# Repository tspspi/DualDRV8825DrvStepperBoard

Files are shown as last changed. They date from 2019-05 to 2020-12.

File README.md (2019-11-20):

# Dual stepper driver board (ATMEGA328P, DRV8825)

This repository contains sourcefiles and schematics for a DRV8825 based
dual stepper driver board. The stepper control algorithm is implemented
on an ATMega328P. The code is compatible with avr-gcc (see Makefile) and
the Arduino IDE (one has to ```#define ARDUINO 1``` to use code for the
Arduino platform).

This controller is thought to be used in robotic and CNC applications.
Some features make it useable as cruise control controller for small
robots that use steppers instead of other brushed or brushless motors
and which may require precise control over speed / sometimes precise control
over their position.

Since the controller uses I2C it can be controlled from 3.3V and 5V
devices without any level shifters (if pullups are only present to 3.3V
but not 5V vcc).

__The controller is currently work in progress (but usable). Functions that
have been tested won't change behaviour__

__Correctness proof is currently work in progress__

The stepper driver can be controlled via I2C and supports:

* Running at a constant speed
* Accelerated linear movement from one position to another
  position (stop to stop) as needed in many CNC applications
* Hold position (enable drivers, no movement)
* Free-wheeling (disable drivers)
* Accelerating or decelerating to another speed
* Emergency stop / Emergency stop with hold

Additional features:

* Commands and status via I2C to support up to 127 stepper
  driver boards (i.e. up to 254 steppers) per I2C bus.
* Runtime modification of acceleration/deceleration as well as
  maximum speed.
* Runtime reconfiguration of microstepping
* A configurable depth command queue (default 10 commands per channel)
* Aborting running commands
* Keeping track of current position (if enabled - useful for CNC applications)
* Keeping track of current speed

* Static analysis using frama-c and ACSL annotation is used to proof that the
  code is free of many known common runtime errors, numeric overflows/underflows,
  does only access valid memory, etc. and fulfills some properties (proofed by
  using an proof assistant). This is currently work in progress.

## Implementation status of I2C commands

|  Command | Implemented | Tested | Description | Comments |
| --- | --- | --- | --- | --- |
| Group 0: Configuration |
| i2cCmd_GetAccelerateDecelerate  	|  Y | Y |  8 byte payload Slave -> Master + 1 Byte Status | |
| i2cCmd_SetAccelerateDecelerate  	|  Y |  |  8 Byte payload Master -> Slave |  | |
| i2cCmd_GetVMax  					|  Y |  |  4 byte payload Slave -> Master + 1 Byte Status |  | |
| i2cCmd_SetVMax  					|  Y |  |  4 Byte payload Mater -> Slave | |
| i2cCmd_GetAlpha  					|  Y |  |  4 Byte payload Slave -> Master + 1 Byte Status | |
| i2cCmd_SetAlpha  					|  Y |  |  4 Byte payload Master -> Slave | |
| i2cCmd_GetMicrostepping  			|  Y |  |  1 Byte payload Slave -> Master (2x 3 Bit) + 1 Byte Status | |
| i2cCmd_SetMicrostepping  			|  Y | Y |  1 Byte payload Master -> Slave | Note: Currently microstepping does __not__ rescale step size (alpha) automatically |
| i2cCmd_GetFault  					|  Y |  |  1 Byte payload Master -> Slave (IS status) | |
| i2cCmd_RecalculateConstants  		|  Y |  |  Used to trigger recalculation of all constants (expensive operation; system should be stopped) | |
| Group 1: Queue |
| i2cCmd_GetCommandQueueSize  		|  Y |  |  Get size (first byte) and unused entires (second byte) of command queue + 1 Byte status | |
| Group 2: Enqueue commands |
| i2cCmd_Queue_Sync  				|  |  |  Sync. point; 1 Byte Channel | |
| i2cCmd_Queue_ConstSpeed  			|  Y | Y |  Constant speed; 1 Byte Channel; 4 Byte Speed | |
| i2cCmd_Queue_MoveTo  				|  Y | Y |  Move To (accelerated); 1 Byte Channel; 4 Byte Position | |
| i2cCmd_Queue_ConstSpeedAccel  	| Y | Y |  Constant speed with acceleration/deceleration; 1 Byte channel; 4 Byte speed | |
| i2cCmd_Queue_Hold  				|  Y | Y |  Hold position; 1 byte channel | |
| i2cCmd_Queue_DisableDrv  			|  Y | Y |  Disable drivers; 1 byte channel (both have to be ordered to disable to be effective) | |
| Group 3: Execute commands immedately |
| i2cCmd_Exec_Sync  				|  |  |  Sync. point; 1 Byte Channel | |
| i2cCmd_Exec_ConstSpeed  			|  Y | Y |  Constant speed; 1 Byte Channel; 4 Byte Speed | |
| i2cCmd_Exec_MoveTo  				|  Y | Y |  Move To (accelerated); 1 Byte Channel; 4 Byte Position | |
| i2cCmd_Exec_ConstSpeedAccel  		| Y | Y |  Constant speed with acceleration/deceleration; 1 Byte channel; 4 Byte speed | |
| i2cCmd_Exec_Hold  				|  Y | Y |  Hold position; 1 byte channel | |
| i2cCmd_Exec_DisableDrv  			|  Y | Y |  Disable drivers; 1 byte channel (both have to be ordered to disable to be effective) | |
| Group F: Emergency commands |
| i2cCmd_EmergencyStop  			|  Y |  |  Keeps motors engaged but stopped | Drivers stay engaged so current will keep flowing |
| i2cCmd_EmergencyOff  				|  Y |  |  Keeps motors disabled | Since drivers are disabled motors are free to turn freely (inertia!) |

## Host library

The host library (controller) has been currenty implemented and tested
on FreeBSD (especially on the RaspberryPi platform). Example usage can
be seen in the ```controller/tests``` directory.

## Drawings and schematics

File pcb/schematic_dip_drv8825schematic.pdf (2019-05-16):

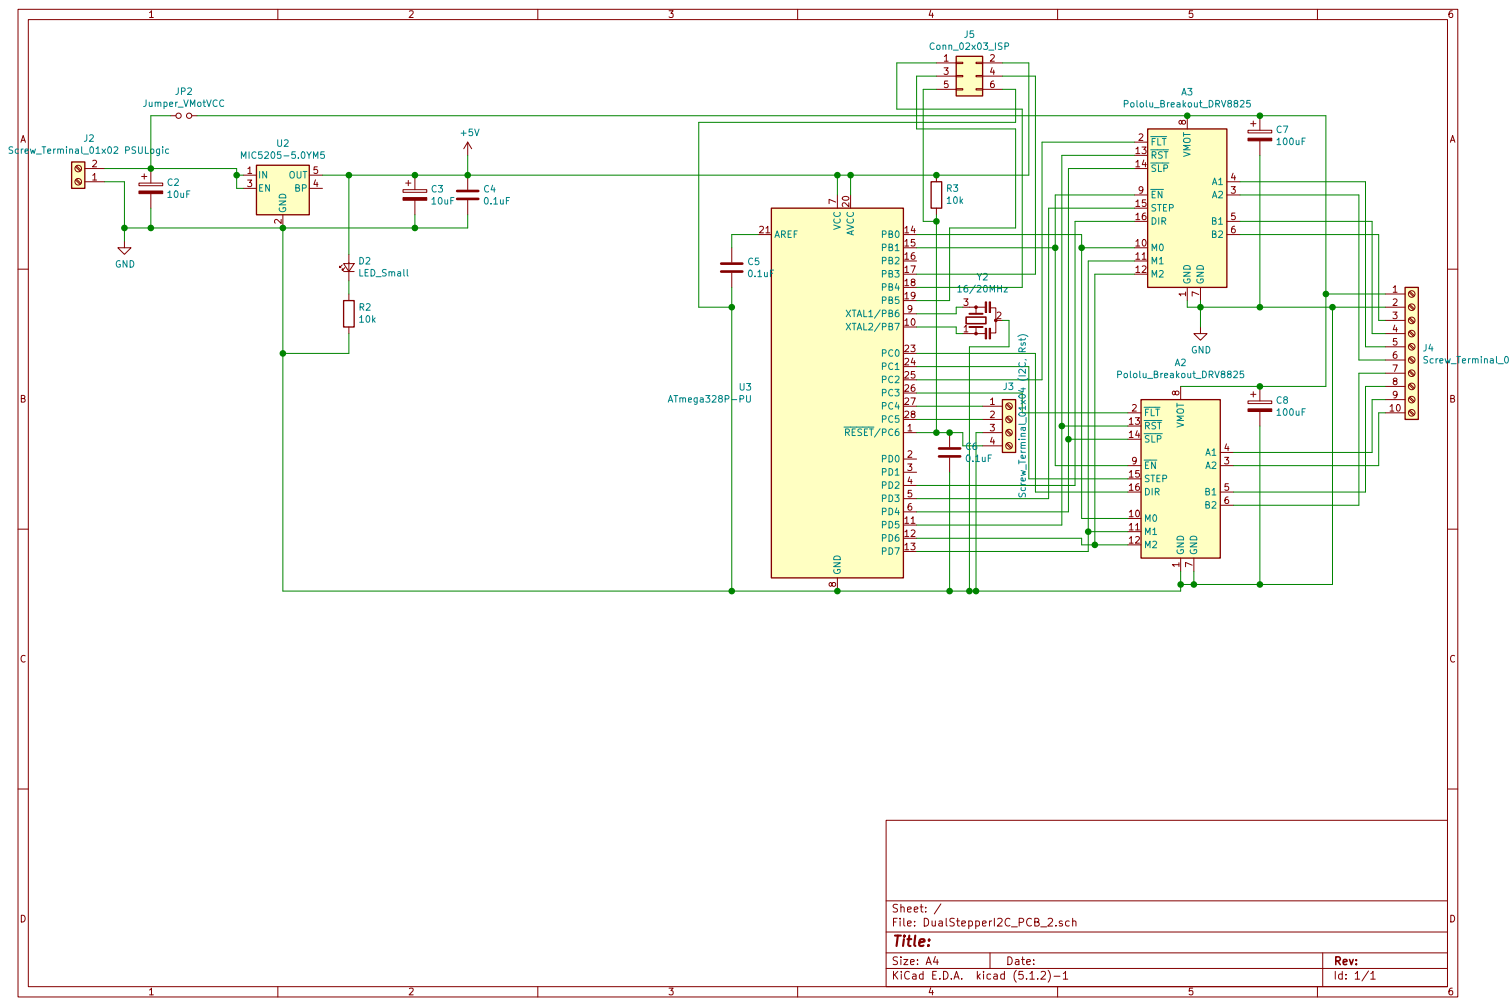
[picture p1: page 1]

1 M0 10 M1 11 M2 12 RST 13 SLP 14 STEP 15 DIR 16 FLT 2 A2 3 A1 4 B1 5 B2 6 GND

4 | J4Screw_Terminal_01x10 (Stepper) GND

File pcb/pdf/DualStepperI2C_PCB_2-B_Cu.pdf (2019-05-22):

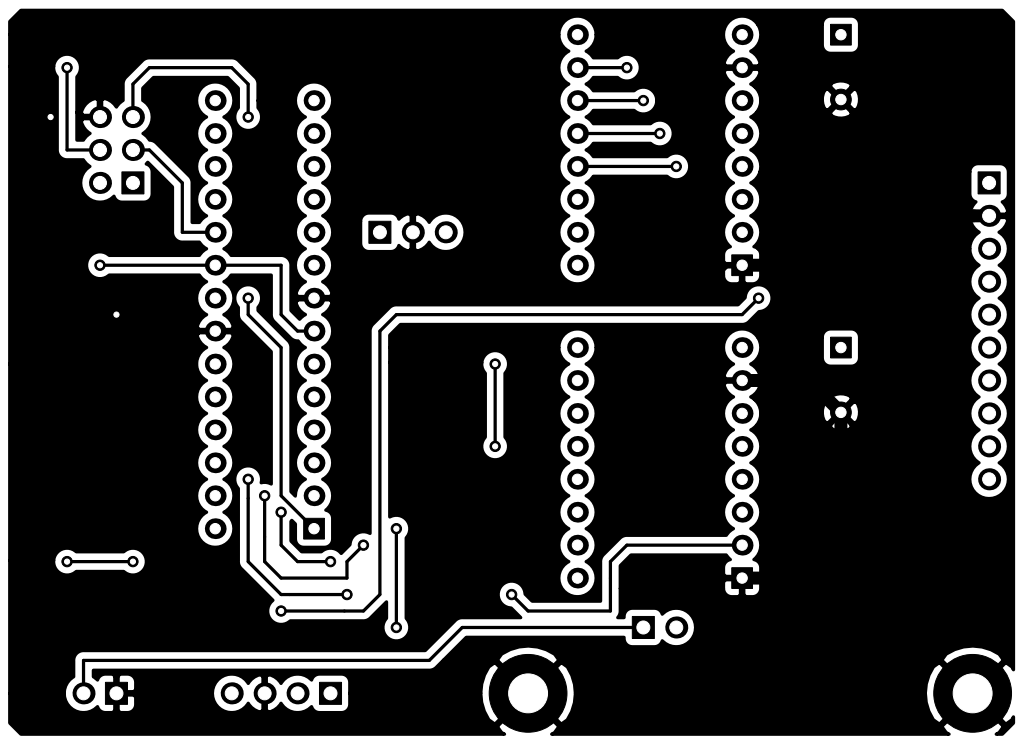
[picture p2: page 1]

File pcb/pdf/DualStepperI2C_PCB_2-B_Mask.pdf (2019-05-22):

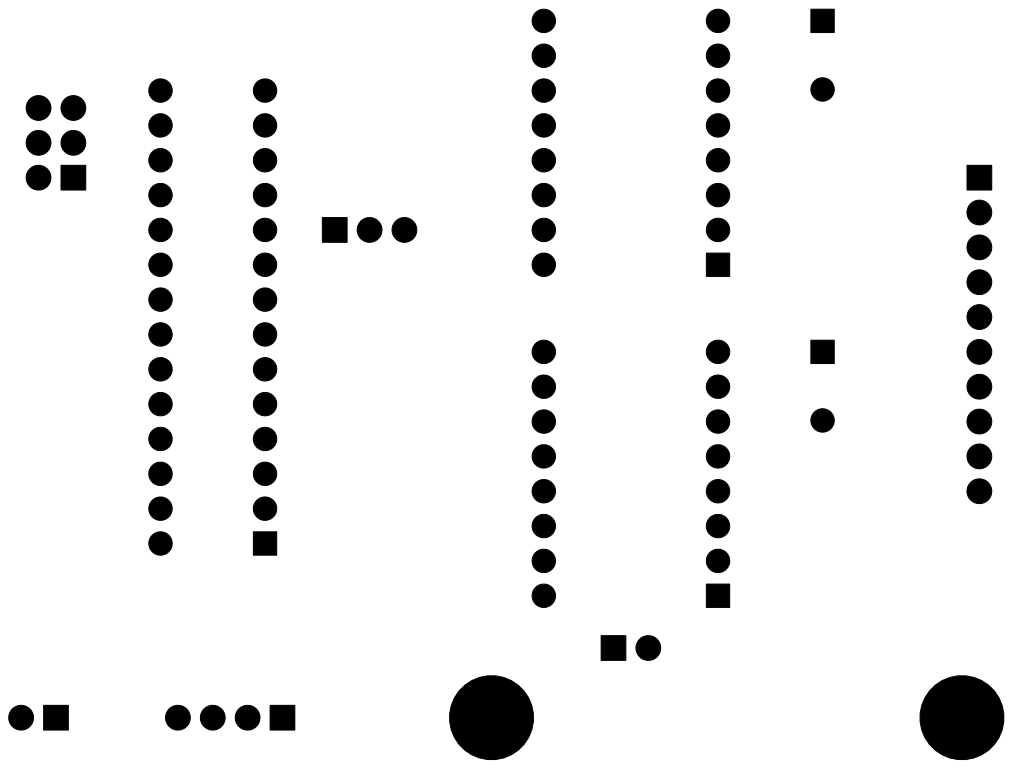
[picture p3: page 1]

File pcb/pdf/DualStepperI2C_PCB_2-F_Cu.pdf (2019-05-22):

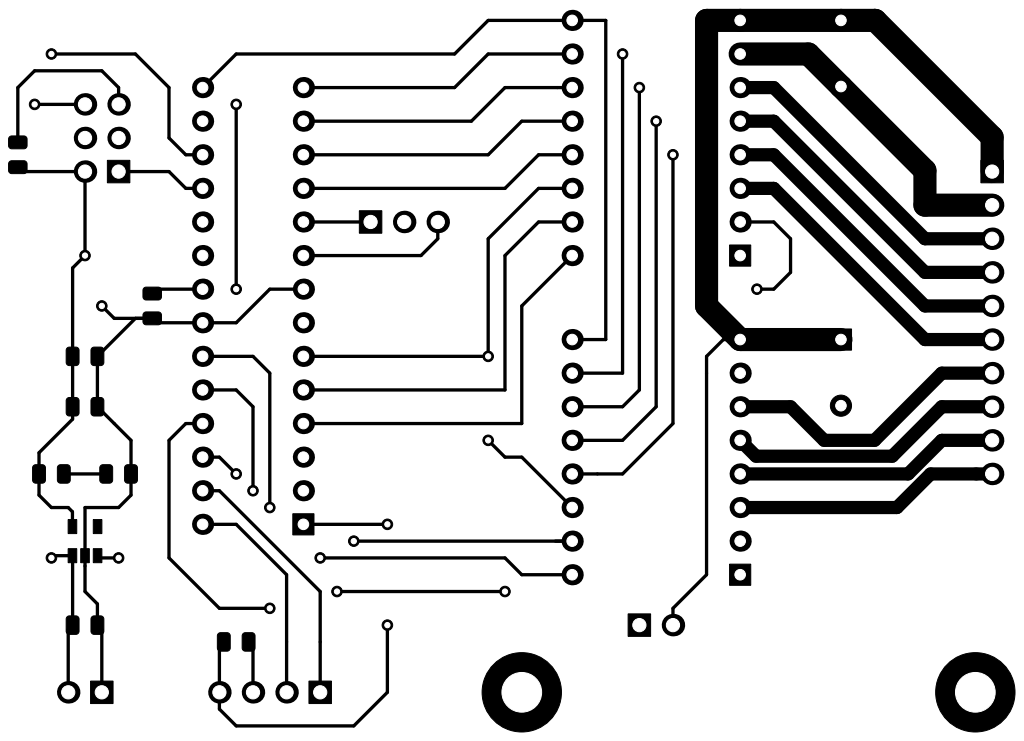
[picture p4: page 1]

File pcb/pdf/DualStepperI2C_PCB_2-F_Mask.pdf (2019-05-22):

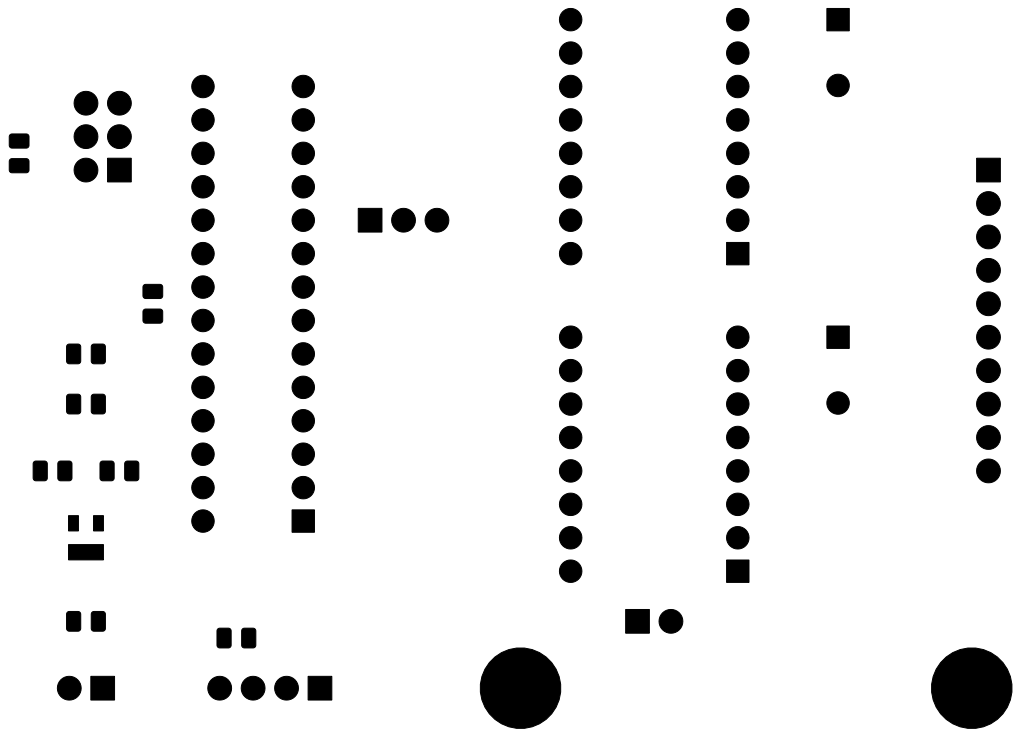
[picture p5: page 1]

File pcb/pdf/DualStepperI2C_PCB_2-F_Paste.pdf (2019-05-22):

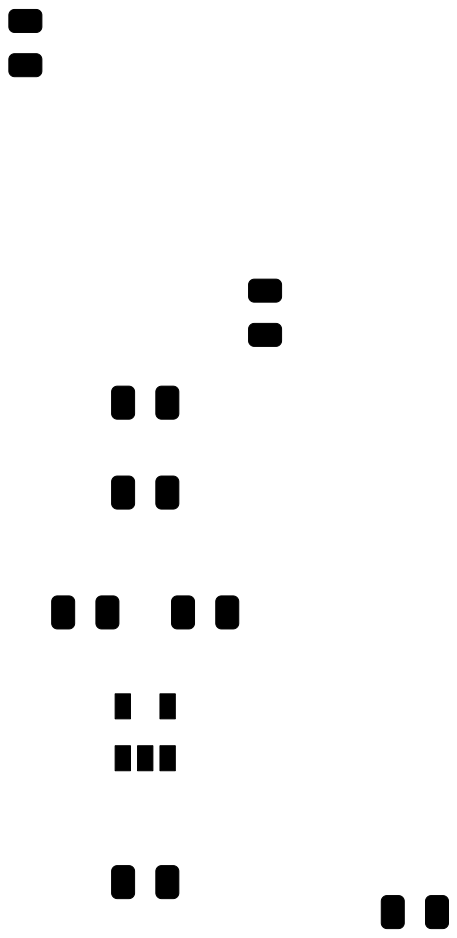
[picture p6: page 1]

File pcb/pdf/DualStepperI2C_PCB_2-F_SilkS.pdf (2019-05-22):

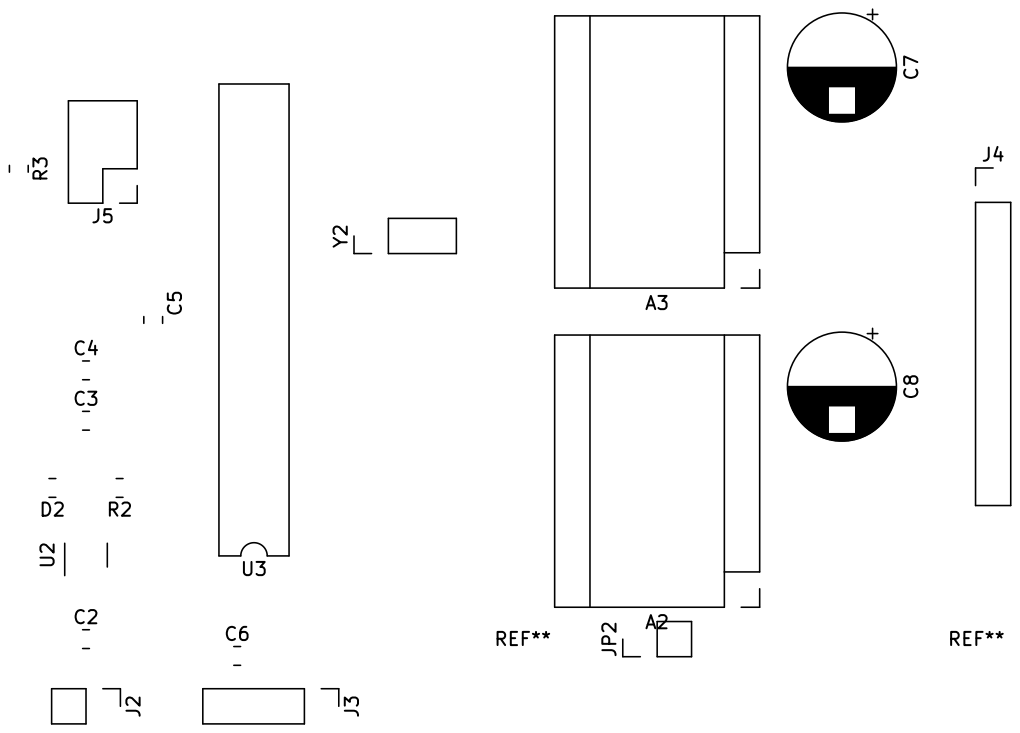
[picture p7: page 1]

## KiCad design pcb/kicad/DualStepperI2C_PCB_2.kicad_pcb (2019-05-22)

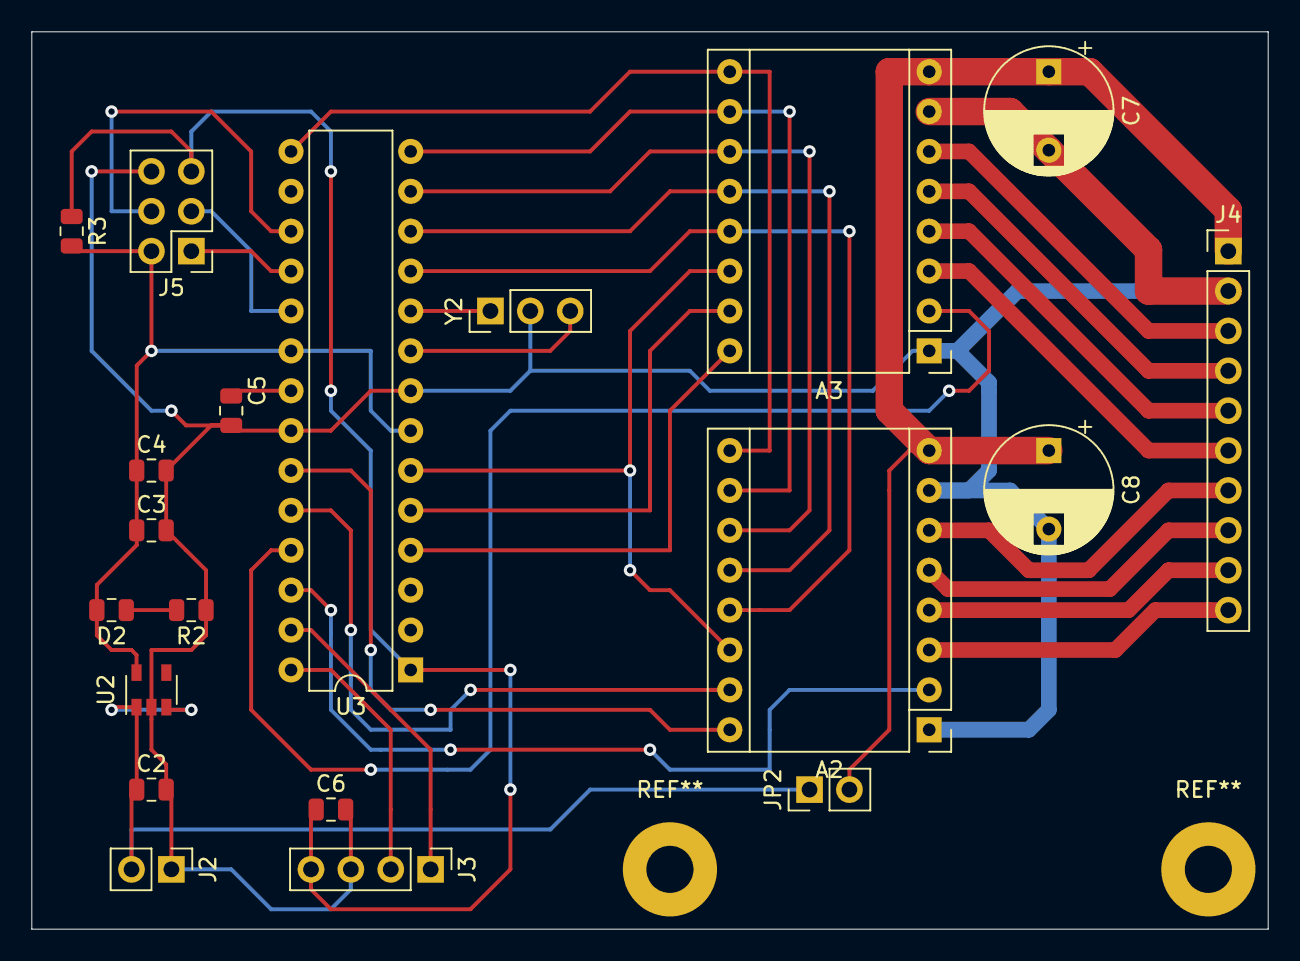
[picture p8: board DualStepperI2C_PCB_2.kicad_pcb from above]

Board: 2 copper layers, 78.7 x 57.1 mm, 20 parts (0 on the bottom side), 34 nets.

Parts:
A2, A3: Pololu_Breakout_DRV8825; Pololu_Breakout-16_15.2x20.3mm
C2, C3: 10uF; C_0805_2012Metric
C4, C5, C6: 0.1uF; C_0805_2012Metric
C7, C8: 100uF; CP_Radial_D8.0mm_P5.00mm
D2: LED_Small; C_0805_2012Metric
J2: Screw_Terminal_01x02 PSULogic; PinHeader_1x02_P2.54mm_Vertical
J3: Screw_Terminal_01x04 (I2C, Rst); PinHeader_1x04_P2.54mm_Vertical
J4: Screw_Terminal_01x10 (Stepper); PinHeader_1x10_P2.54mm_Vertical
J5: Conn_02x03_ISP; PinHeader_2x03_P2.54mm_Vertical
JP2: Jumper_VMotVCC; PinHeader_1x02_P2.54mm_Vertical
R2, R3: 10k; R_0805_2012Metric
U2: MIC5205-5.0YM5; SOT-23-5
U3: ATmega328P-PU; DIP-28_W7.62mm
Y2: 16/20MHz; PinHeader_1x03_P2.54mm_Vertical

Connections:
+5V: C3.1, C4.1, D2.2, J5.2, R3.2, U2.5, U3.7, U3.20
GND: A2.1, A2.7, A3.1, A3.7, C2.2, C3.2, C4.2, C5.2, C6.2, C7.2, C8.2, J2.1, J3.3, J4.2, J5.6, R2.1, U2.2, U3.8, U3.22, Y2.2
unnamed: A2.2, U3.26
unnamed: A2.3, J4.10
unnamed: A2.4, J4.9
unnamed: A2.5, J4.8
unnamed: A2.6, J4.7
unnamed: A2.8, A3.8, C7.1, C8.1, J4.1, JP2.2
unnamed: A2.9, A3.9, U3.15
unnamed: A2.10, A3.10, U3.14
unnamed: A2.11, A3.11, U3.13
unnamed: A2.12, A3.12, U3.12
unnamed: A2.13, A3.13, U3.11
unnamed: A2.14, A3.14, U3.6
unnamed: A2.15, U3.24
unnamed: A2.16, U3.23
unnamed: A3.2, U3.25
unnamed: A3.3, J4.6
unnamed: A3.4, J4.5
unnamed: A3.5, J4.4
unnamed: A3.6, J4.3
unnamed: A3.15, U3.5
unnamed: A3.16, U3.4
unnamed: C2.1, J2.2, JP2.1, U2.1, U2.3
unnamed: C5.1, U3.21
unnamed: C6.1, J3.4, J5.5, R3.1, U3.1
unnamed: D2.1, R2.2
unnamed: J3.1, U3.27
unnamed: J3.2, U3.28
unnamed: J5.1, U3.18
unnamed: J5.3, U3.19
unnamed: J5.4, U3.17
unnamed: U3.9, Y2.3
unnamed: U3.10, Y2.1

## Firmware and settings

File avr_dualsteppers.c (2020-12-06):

#include <avr/io.h>
#include <avr/interrupt.h>
#include <math.h>
#include <util/twi.h>
#include <stdint.h>

#define DEBUG

#ifndef STEPPER_I2C_ADDRESS
	#define STEPPER_I2C_ADDRESS 0x14
#endif
#ifndef M_PI
	#define M_PI 3.14159265358979323846264338327950288
#endif

/*
	If the following preprocessor directive is defined the steppers
	will be put in sleep mode upon reset (after initial power-up)
*/
#define STEPPER_DISABLE_STARTUP 1

#ifndef __cplusplus
	typedef int bool;
	#define true 1
	#define false 0
#endif

/*
	Pin usage:
		pinDir1		2	PD2		OUT
		pinStep1	3	PD3		OUT

		pinFault1	16	PC2		IN		PCINT10 (PCI1)
		pinDir2		14	PC0		OUT
		pinStep2	15	PC1		OUT
		pinFault2	17	PC3		IN		PCINT11 (PCI1)

		pinSleep    4	PD4		OUT
		pinReset    5	PD5		OUT
		pinMode2    6	PD6		OUT
		pinMode1    7	PD7		OUT

		pinMode0    8	PB0		OUT
		pinEnable   9	PB1		OUT


	I/O bank configuration:
		PB:		0	OUT		LOW (Fullstep)
				1	OUT		HIGH (ENABLE)
				2	IN		no pull
				3	IN		no pull
				4	IN		no pull
				5	IN		no pull
				6	IN		no pull
				7	IN		no pull

				DDRB = 0x03;
				PORTB = 0x02;

		PC:		0	OUT		LOW
				1	OUT		LOW
				2	IN		no pull
				3	IN		no pull
				4	IN		no pull
				5	IN		no pull
				6	IN		no pull
				7	IN		no pull

				DDRC = 0x03;
				PORTC = 0x00;

		PD:		0	IN		no pull
				1	IN		no pull
				2	OUT		LOW (Dir)
				3	OUT		LOW (Step)
				4	OUT		LOW (SLEEP)
				5	OUT		LOW (RESET)
				6	OUT		LOW (Fullstep)
				7	OUT		LOW (Fullstep)

				DDRD = 0xFC;
				PORTD = 0x00;
*/

/*
	Master clock source will be TIMER2

	Running with one of the following settings:
		Prescaler		Frequency		OCR1A		Effective Pulse Frequency
		/64				250 kHz			2			62.5 kHz
		/256			62.5 kHz		1			31.2 kHz
		/1024			15.625 kHz		1			7.812 kHz
*/

#ifndef STEPPER_COMMANDQUEUELENGTH
	#define STEPPER_COMMANDQUEUELENGTH 10
#endif

#define STEPPER_TIMERTICK_FRQ 			7812/2
#define STEPPER_TIMERTICK_PRESCALER		0x06
#define STEPPER_TIMERTICK_OVERFLOWVAL	0x01
#define STEPPER_WAKEUP_SLEEP_TICKS		10			/* More than 1.2 ms! */

/*
#define STEPPER_INITIAL_ALPHA			(0.01 * M_PI)
#define STEPPER_INITIAL_VMAX			(83.0 * M_PI)
#define STEPPER_INITIAL_ACCELERATION	(18.0 * M_PI)
#define STEPPER_INITIAL_DECELERATION	(-18.0 * M_PI)
*/
#define STEPPER_INITIAL_ALPHA			(0.01 * M_PI)
#define STEPPER_INITIAL_VMAX			6
#define STEPPER_INITIAL_ACCELERATION	1 /* 6 */
#define STEPPER_INITIAL_DECELERATION	-1 /* -6 */
#define STEPPER_INITIAL_MICROSTEPPING	0

/*
	Min and max configureable values
		Alpha:		Step size in radians
		V_max:		Maximum speed in radians per second
					Note: Since max. 250 kHz stepping frequency
						is supported by DRV8825 we use this as
						the limit together with alpha.

						(Alpha * 250 000)
		a, d		Acceleration and deceleration in radians per
					squaresecond
*/
#define STEPPER_MAX_ALPHA					(0.01 * M_PI)
#define STEPPER_MIN_ALPHA					((0.01 * M_PI)/128.0)
#define STEPPER_MAX_VMAX					100 /* (STEPPER_MAX_ALPHA * 250000.0) */
#define STEPPER_MIN_VMAX					0.01
// #define STEPPER_MIN_ACCELERATION			0.01 /* Currently arbitrary! */
// #define STEPPER_MAX_ACCELERATION			((STEPPER_MAX_VMAX * STEPPER_MAX_VMAX)/(STEPPER_MIN_ALPHA*4294967296.0))
#define STEPPER_MIN_ACCELERATION			((STEPPER_MAX_VMAX * STEPPER_MAX_VMAX)/(STEPPER_MIN_ALPHA*4294967296.0))
#define STEPPER_MAX_ACCELERATION			1000 /* Currently arbitrary */
#define STEPPER_MIN_DECELERATION			(-1.0 * ((STEPPER_MAX_VMAX * STEPPER_MAX_VMAX)/(STEPPER_MIN_ALPHA*4294967296.0)))
#define STEPPER_MAX_DECELERATION			-0.01 /* Currently arbitrary! */

#define STEPPER_MIN_RELATIVEDISTANCE		STEPPER_MIN_ALPHA
#define STEPPER_MAX_RELATIVEDISTANCE		(4294967295.0 * STEPPER_MIN_ALPHA)

/*
	We use our own systick implementation
*/
unsigned long int millis();
unsigned long int micros();
void delay(unsigned long millisecs);
void delayMicros(unsigned int microDelay);

enum stepperCommandType {
	stepperCommand_AccelerateStopToStop,
	stepperCommand_ConstantSpeed,
	stepperCommand_Stop,
	stepperCommand_Disable,
	stepperCommand_AccelerateToSpeed,
	stepperCommand_DecelerateToSpeed,
};

struct stepperCommand {
	enum stepperCommandType		cmdType;
	int 						forward;
	union {
		struct {
			uint32_t			nA;
			uint32_t			nC;
			uint32_t			nD;

			double				c7, c8, c9; /* Calculation constants for our specific acceleration and deceleration. */

			double				initialDelayTicks;
		} acceleratedStopToStop;
		struct {
			uint32_t			cConst; /* In case of constant speed mode we supply the tick count per constant step */
		} constantSpeed;
		struct {
			uint32_t			nA;
			uint32_t			nD;

			double				c8, c9;
			double				cEnd;
			double				cStart;
		} accelerateDecelerateToConstSpeed;
	} data;
};

/*
	Command queue is a ringbuffer. Head points always to the next entry
	that is available for writing. If head == tail the queue is EMPTY!

	Tail is only ever advanced by TIMER2_COMPA_vect, head only ever by
	the motion planner.

	If Head + 1 == Tail the queue is currently FULL and nothing can
	be enqueued.
*/
struct stepperState {
	double							c_i;				/* The previously loaded c_i (used during calculation and advancing) */
	uint32_t						counterCurrent;		/* Counter reduced every time until we reach zero */

	struct stepperCommand			cmdQueue[STEPPER_COMMANDQUEUELENGTH];
	unsigned int					cmdQueueHead;
	unsigned int					cmdQueueTail;

	#ifdef ENABLE_ABSOLUTEPOSITION
		long int						currentPosition;			/* Current position in "steps" i.e. currentPosition * alpha = angular Position */
	#endif

	/* Cache for precalculated constants - see documentation */
	struct {
		double						c1;
		double						c2;
		double						c3;
		double						c4;
		double						c5;

		double						c7;
		double						c8;
		double						c9;
		double						c10;
	} constants;

	struct {
		double						acceleration; /* in rad/sec */
		double						deceleration; /* in rad/sec */
		double						alpha; /* step size in rad */
		double						vmax; /* in rad/sec */
	} settings;
};

#define STEPPER_COUNT 2

/*
	Declare state for both steppers
*/
static struct stepperState			state[STEPPER_COUNT];
static uint8_t						stateMicrostepping;
volatile static uint8_t				stateFault;
static uint8_t						drvEnableState;
static uint8_t						drvRealEnabled;

bool bResetRun = false;
static volatile bool bIntTriggered = false;

/*@
	requires \valid(&PORTC) && \valid(&PORTD);

	assigns drvRealEnabled;
	assigns bIntTriggered;

	assigns PORTC, PORTD;

	ensures
		\forall integer iStep; 0 <= iStep < STEPPER_COUNT
		==> (state[iStep].cmdQueueHead >= 0) && (state[iStep].cmdQueueHead < STEPPER_COMMANDQUEUELENGTH);
	ensures
		\forall integer iStep; 0 <= iStep < STEPPER_COUNT
		==> (state[iStep].cmdQueueTail >= 0) && (state[iStep].cmdQueueTail < STEPPER_COMMANDQUEUELENGTH);
*/
static void handleTimer2Interrupt() {
	if(!bIntTriggered) {
		return;
	}
	bIntTriggered = false;

	/*
		Re-enable counter. This is used to delay the
		next stepper commands after re-awaking from
		sleep.
	*/
	if((drvRealEnabled & 0x7F) != 0) {
		drvRealEnabled = drvRealEnabled - 1;
		return;
	}

	/*
		Interrupt handler executed with 2 * STEPPER_TIMERTICK_FRQ frequency
		either use to disable step pins or advance state machine depending on
		out state. We have to finish in way less then 1024 ticks ...
	*/
	int stepperIdx;
	/*@
		loop assigns PORTD, PORTC;
		loop assigns drvRealEnabled, drvEnableState;
		loop assigns state[0 .. (STEPPER_COUNT-1)];

		loop invariant 0 <= stepperIdx < STEPPER_COUNT;

	*/
	for(stepperIdx = 0; stepperIdx < STEPPER_COUNT; stepperIdx = stepperIdx + 1) {
		if(bResetRun) {
			if(stepperIdx == 0) {
				// Pulse PD2 low
				PORTD = PORTD & (~0x08);
			} else {
				// Pulse PC1 low
				PORTC = PORTC & (~0x02);
			}

			if((drvEnableState == 0) && ((drvRealEnabled & 0x80) != 0)) {
				/* Put driver into sleep if none is enabled AND our current real enable state is not the same */
				drvRealEnabled = drvRealEnabled & 0x7F;
				PORTD = PORTD & (~0x10); /* Enter sleep state by pulling SLEEP LOW (enabled) */
			}
		} else {
			if(state[stepperIdx].cmdQueueTail == state[stepperIdx].cmdQueueHead) {
				/* Nothing to do ... */
				continue;
			}

			const int qIdx = state[stepperIdx].cmdQueueTail;
			if(state[stepperIdx].c_i == -1) {
				/* We wake up from idle ... any may have to do some initialization */
				if(stepperIdx == 0) {
					// PD2
					if(state[stepperIdx].cmdQueue[qIdx].forward != 0) {
						PORTD = PORTD | 0x04;
					} else {
						PORTD = PORTD & (~0x04);
					}
				} else {
					// PC0
					if(state[stepperIdx].cmdQueue[qIdx].forward != 0) {
						PORTC = PORTC | 0x01;
					} else {
						PORTC = PORTC & (~0x01);
					}
				}

				/* Check if drivers are disabled and we have to execute an command ... */
				if((drvRealEnabled & 0x80) == 0) {
					/* Steppers are disabled. Re-enable and wait for startup period */
					PORTD = PORTD | 0x10; /* Leave sleep state by pulling SLEEP HIGH (disabled) */
					drvRealEnabled = 0x80 | STEPPER_WAKEUP_SLEEP_TICKS;
					drvEnableState = drvEnableState | (1 << stepperIdx);
					break; // Next stepper as usual
				}

				if(state[stepperIdx].cmdQueue[qIdx].cmdType == stepperCommand_AccelerateStopToStop) {
					state[stepperIdx].c_i = state[stepperIdx].cmdQueue[qIdx].data.acceleratedStopToStop.initialDelayTicks;
					if(state[stepperIdx].c_i > 4294967295.0) {
						state[stepperIdx].counterCurrent = ~0;
					} else if(state[stepperIdx].c_i < 1.0) {
						state[stepperIdx].counterCurrent = 1;
					} else {
						state[stepperIdx].counterCurrent = (uint32_t)state[stepperIdx].c_i;
					}
				} else if(state[stepperIdx].cmdQueue[qIdx].cmdType == stepperCommand_ConstantSpeed) {
					state[stepperIdx].c_i = state[stepperIdx].cmdQueue[qIdx].data.constantSpeed.cConst;
					state[stepperIdx].counterCurrent = state[stepperIdx].cmdQueue[qIdx].data.constantSpeed.cConst;
				} else if(state[stepperIdx].cmdQueue[qIdx].cmdType == stepperCommand_Disable) {
					drvEnableState = drvEnableState & (~(0x01 << stepperIdx));
					/* Switch to next state at next interrupt */
					state[stepperIdx].cmdQueueTail = (state[stepperIdx].cmdQueueTail + 1) % STEPPER_COMMANDQUEUELENGTH;
					state[stepperIdx].c_i = -1; /* This will initialize the next state as soon as it is available */
					continue;
				} else if(state[stepperIdx].cmdQueue[qIdx].cmdType == stepperCommand_Stop) {
					/*
						Our driver has already been enabled since we do that whenever we
						reach an enqueued command. So simply remove this task from the task
						queue. As long as nothing has been enqueued the steppers will be
						engaged and stopped
					*/
					state[stepperIdx].cmdQueueTail = (state[stepperIdx].cmdQueueTail + 1) % STEPPER_COMMANDQUEUELENGTH;
					state[stepperIdx].c_i = -1; /* This will initialize the next state as soon as it is available */
					continue;
				} else if((state[stepperIdx].cmdQueue[qIdx].cmdType == stepperCommand_AccelerateToSpeed) || (state[stepperIdx].cmdQueue[qIdx].cmdType == stepperCommand_DecelerateToSpeed)) {
					state[stepperIdx].c_i = state[stepperIdx].cmdQueue[qIdx].data.accelerateDecelerateToConstSpeed.cStart;
					if(state[stepperIdx].c_i > 4294967295.0) {
						state[stepperIdx].counterCurrent = ~0;
					} else if(state[stepperIdx].c_i < 1.0) {
						state[stepperIdx].counterCurrent = 1;
					} else {
						state[stepperIdx].counterCurrent = (uint32_t)state[stepperIdx].c_i;
					}
				} else {
					continue;
				}
			} else if((state[stepperIdx].counterCurrent = state[stepperIdx].counterCurrent - 1) > 0) {
				/* Just advance our counter ... */
				continue;
			} else if(state[stepperIdx].cmdQueue[qIdx].cmdType == stepperCommand_AccelerateStopToStop) {
				if(state[stepperIdx].cmdQueue[qIdx].data.acceleratedStopToStop.nA > 0) {
					state[stepperIdx].c_i = state[stepperIdx].c_i / (1 + state[stepperIdx].constants.c8 * state[stepperIdx].c_i * state[stepperIdx].c_i);
					state[stepperIdx].cmdQueue[qIdx].data.acceleratedStopToStop.nA = state[stepperIdx].cmdQueue[qIdx].data.acceleratedStopToStop.nA - 1;

					/* c_i to counter value */
					if(state[stepperIdx].c_i > 4294967295.0) {
						state[stepperIdx].counterCurrent = ~0;
					} else if(state[stepperIdx].c_i < 1.0) {
						state[stepperIdx].counterCurrent = 1;
					} else {
						state[stepperIdx].counterCurrent = (uint32_t)state[stepperIdx].c_i;
					}
				} else if(state[stepperIdx].cmdQueue[qIdx].data.acceleratedStopToStop.nC > 0) {
					state[stepperIdx].cmdQueue[qIdx].data.acceleratedStopToStop.nC = state[stepperIdx].cmdQueue[qIdx].data.acceleratedStopToStop.nC - 1;

					/* c_i to counter value */
					if(state[stepperIdx].c_i > 4294967295.0) {
						state[stepperIdx].counterCurrent = ~0;
					} else if(state[stepperIdx].c_i < 1.0) {
						state[stepperIdx].counterCurrent = 1;
					} else {
						state[stepperIdx].counterCurrent = (uint32_t)state[stepperIdx].c_i;
					}
				} else if(state[stepperIdx].cmdQueue[qIdx].data.acceleratedStopToStop.nD > 0) {
					state[stepperIdx].c_i = state[stepperIdx].c_i / (1 + state[stepperIdx].constants.c9 * state[stepperIdx].c_i * state[stepperIdx].c_i);
					/* c_i to counter value */
					if(state[stepperIdx].c_i > 4294967295.0) {
						state[stepperIdx].counterCurrent = ~0;
					} else if(state[stepperIdx].c_i < 1.0) {
						state[stepperIdx].counterCurrent = 1;
					} else {
						state[stepperIdx].counterCurrent = (uint32_t)state[stepperIdx].c_i;
					}

					if((state[stepperIdx].cmdQueue[qIdx].data.acceleratedStopToStop.nD = state[stepperIdx].cmdQueue[qIdx].data.acceleratedStopToStop.nD - 1) == 0) {
						/* Switch to next state at next interrupt */
						state[stepperIdx].cmdQueueTail = (state[stepperIdx].cmdQueueTail + 1) % STEPPER_COMMANDQUEUELENGTH;
						state[stepperIdx].c_i = -1; /* This will initialize the next state as soon as it is available */
					}
				}
			} else if(state[stepperIdx].cmdQueue[qIdx].cmdType == stepperCommand_AccelerateToSpeed) {
				state[stepperIdx].c_i = state[stepperIdx].c_i / (1 + state[stepperIdx].constants.c8 * state[stepperIdx].c_i * state[stepperIdx].c_i);

				/* c_i to counter value */
				if(state[stepperIdx].c_i > 4294967295.0) {
					state[stepperIdx].counterCurrent = ~0;
				} else if(state[stepperIdx].c_i < 1.0) {
					state[stepperIdx].counterCurrent = 1;
				} else {
					state[stepperIdx].counterCurrent = (uint32_t)state[stepperIdx].c_i;
				}

				if((state[stepperIdx].cmdQueue[qIdx].data.accelerateDecelerateToConstSpeed.nA = state[stepperIdx].cmdQueue[qIdx].data.accelerateDecelerateToConstSpeed.nA - 1) == 0) {
					/* Switch to next state at next interrupt */
					state[stepperIdx].cmdQueueTail = (state[stepperIdx].cmdQueueTail + 1) % STEPPER_COMMANDQUEUELENGTH;
					state[stepperIdx].c_i = -1; /* This will initialize the next state as soon as it is available */
				}
			} else if(state[stepperIdx].cmdQueue[qIdx].cmdType == stepperCommand_DecelerateToSpeed) {
				state[stepperIdx].c_i = state[stepperIdx].c_i / (1 + state[stepperIdx].constants.c9 * state[stepperIdx].c_i * state[stepperIdx].c_i);

				/* c_i to counter value */
				if(state[stepperIdx].c_i > 4294967295.0) {
					state[stepperIdx].counterCurrent = ~0;
				} else if(state[stepperIdx].c_i < 1.0) {
					state[stepperIdx].counterCurrent = 1;
				} else {
					state[stepperIdx].counterCurrent = (uint32_t)state[stepperIdx].c_i;
				}

				if((state[stepperIdx].cmdQueue[qIdx].data.accelerateDecelerateToConstSpeed.nD = state[stepperIdx].cmdQueue[qIdx].data.accelerateDecelerateToConstSpeed.nD - 1) == 0) {
					/* Switch to next state at next interrupt */
					state[stepperIdx].cmdQueueTail = (state[stepperIdx].cmdQueueTail + 1) % STEPPER_COMMANDQUEUELENGTH;
					state[stepperIdx].c_i = -1; /* This will initialize the next state as soon as it is available */
				}
			} else if(state[stepperIdx].cmdQueue[qIdx].cmdType == stepperCommand_ConstantSpeed) {
				state[stepperIdx].counterCurrent = state[stepperIdx].c_i; // Counter reload ...
			}

			if(stepperIdx == 0) {
				// Pulse PD2 high
				PORTD = PORTD | 0x08;
				#ifdef ENABLE_ABSOLUTEPOSITION
					if((PORTD & 0x04) != 0) {
						if(state[0].currentPosition < 2147483647) {
							state[0].currentPosition++;
						}
					} else {
						if(state[0].currentPosition > 0) {
							state[0].currentPosition--;
						}
					}
				#endif
			} else {
				// Pulse PC1 high
				PORTC = PORTC | 0x02;
				#ifdef ENABLE_ABSOLUTEPOSITION
					if((PORTC & 0x01) != 0) {
						if(state[1].currentPosition < 2147483647) {
							state[1].currentPosition++;
						}
					} else {
						if(state[1].currentPosition > 0) {
							state[1].currentPosition--;
						}
					}
				#endif
			}
		}
	}
	bResetRun = !bResetRun;
}

/*@
	assigns bIntTriggered;
	ensures bIntTriggered == true;
*/
ISR(TIMER2_COMPA_vect) {
	bIntTriggered = true;
}

/*@
	requires \valid_read(&PINC);

	assigns stateFault;
*/
ISR(PCINT1_vect) {
	/*
		Update fault pins ...
	*/
	uint8_t faultPins = PINC;
	stateFault = stateFault | (((faultPins >> 2) & 0x01) ^ 0x01) | (((faultPins >> 2) & 0x02) ^ 0x02);
}
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
int main() {
	#ifndef FRAMAC_SKIP
		cli();
	#endif

	// Setup TIMER0 as our sysclk timer
	// TCCR0A = 0x02;		/* CTC mode */
	TCCR0A = 0x00;
	TCCR0B = 0x03;		/* /64 prescaler */
	TIMSK0 = 0x01;		/* Enable overflow interrupt */

	// Sysclk is now working - re-enable interrupts
	sei();

	#ifdef DEBUG
		// Signal bootup via LED
		DDRB = 0x20;
		PORTB = 0x20;
		delay(1000);
		PORTB = 0x00;
		delay(1000);
		PORTB = 0x20;
		delay(1000);
		PORTB = 0x00;
		delay(1000);
	#endif

	// Disable serial (enabled from bootloader)
	UCSR0B = 0;

	// Initialize I2C
	i2cSlaveInit(STEPPER_I2C_ADDRESS);

	// Stepper setup
	stepperSetup();

	/*
		Since we don't use "delay" in production any more we
		can disable TIMER0 again to reduce possible jitter
		of TIMER2.
	*/
	#ifndef DEBUG
		TIMSK0 = 0x00; /* Disable interrupts of TIMER0 */
	#endif

	for(;;) {
		/*
			Handle stepper events (NOT from ISR but synchronously)
		*/
		handleTimer2Interrupt();
		/*
			Execute I2C message loop
		*/
		i2cMessageLoop();
	}
}

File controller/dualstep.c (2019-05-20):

#include <stdlib.h>

#include "./dualstep.h"

#include <stdint.h>
#include <math.h>

#include "./serdeshelper.h"

#ifdef __cplusplus
	extern "C" {
#endif

enum stepperI2cCommand {
	i2cCmd_GetAccelerateDecelerate		= 0x01,	/* 8 byte payload Slave -> Master + 1 Byte Status */
	i2cCmd_SetAccelerateDecelerate		= 0x02,	/* 8 Byte payload Master -> Slave */
	i2cCmd_GetVMax						= 0x03, /* 4 byte payload Slave -> Master + 1 Byte Status */
	i2cCmd_SetVMax						= 0x04,	/* 4 Byte payload Mater -> Slave */
	i2cCmd_GetAlpha						= 0x05,	/* 4 Byte payload Slave -> Master + 1 Byte Status */
	i2cCmd_SetAlpha						= 0x06,	/* 4 Byte payload Master -> Slave */
	i2cCmd_GetMicrostepping				= 0x07, /* 1 Byte payload Slave -> Master (2x 3 Bit) + 1 Byte Status */
	i2cCmd_SetMicrostepping				= 0x08, /* 1 Byte payload Master -> Slave */

	i2cCmd_GetFault						= 0x0E, /* 1 Byte payload Master -> Slave (IS status) */
	i2cCmd_RecalculateConstants			= 0x0F, /* Used to trigger recalculation of all constants (expensive operation; system should be stopped) */



	i2cCmd_GetCommandQueueSize			= 0x10,	/* Get size (first byte) and unused entires (second byte) of command queue + 1 Byte status */



	i2cCmd_Queue_Sync					= 0x20,	/* Sync. point; 1 Byte Channel */
	i2cCmd_Queue_ConstSpeed				= 0x21,	/* Constant speed; 1 Byte Channel; 4 Byte Speed */
	i2cCmd_Queue_MoveTo					= 0x22,	/* Move To (accelerated); 1 Byte Channel; 4 Byte Position */
	i2cCmd_Queue_ConstSpeedAccel		= 0x23,	/* Constant speed with acceleration/deceleration; 1 Byte channel; 4 Byte speed */
	i2cCmd_Queue_Hold					= 0x2E,	/* Hold position; 1 byte channel */
	i2cCmd_Queue_DisableDrv				= 0x2F,	/* Disable drivers; 1 byte channel (both have to be ordered to disable to be effective) */

	i2cCmd_Exec_Sync					= 0x30,	/* Sync. point; 1 Byte Channel */
	i2cCmd_Exec_ConstSpeed				= 0x31,	/* Constant speed; 1 Byte Channel; 4 Byte Speed */
	i2cCmd_Exec_MoveTo					= 0x32,	/* Move To (accelerated); 1 Byte Channel; 4 Byte Position */
	i2cCmd_Exec_ConstSpeedAccel			= 0x33,	/* Constant speed with acceleration/deceleration; 1 Byte channel; 4 Byte speed */
	i2cCmd_Exec_Hold					= 0x3E,	/* Hold position; 1 byte channel */
	i2cCmd_Exec_DisableDrv				= 0x3F,	/* Disable drivers; 1 byte channel (both have to be ordered to disable to be effective) */

	i2cCmd_EmergencyStop				= 0xFE,	/* Keeps motors engaged but stopped */
	i2cCmd_EmergencyOff					= 0xFF, /* Keeps motors disabled */
};


static enum i2cDualStepperError i2cDual_Release(
	struct i2cDualStepper* lpSelf
) {
	if(lpSelf == NULL) { return i2cDualStepperErrorE_InvalidParam; }

	/*
		We do NOT stop, disengage drivers, etc. if not
		told explicitly!
	*/
	free(lpSelf);
	return i2cDualStepperErrorE_Ok;
}

static enum i2cDualStepperError i2cDual_GetAccelerationDeceleration(
	struct i2cDualStepper* lpSelf,
	unsigned long int dwChannel,
	double* lpAcceleration,
	double* lpDeceleration
) {
	enum i2cError i2e;

	if(lpSelf == NULL) { return i2cDualStepperErrorE_InvalidParam; }
	if(dwChannel > 1) { return i2cDualStepperErrorE_InvalidParam; }

	uint8_t req[2] = { i2cCmd_GetAccelerateDecelerate, (uint8_t)dwChannel };
	uint8_t resp[8];

	/* Perform query */
	i2e = i2cWriteRead(lpSelf->i2cBus, lpSelf->devAddr, req, sizeof(req), resp, sizeof(resp));
	if(i2e != i2cE_Ok) { return i2cDualStepperErrorE_IOError; }

	if(lpAcceleration != NULL) { (*lpAcceleration) = (double)deserializeIEEE754SingleFloat_4Bytes(&(resp[0])); }
	if(lpDeceleration != NULL) { (*lpDeceleration) = (double)deserializeIEEE754SingleFloat_4Bytes(&(resp[4])); }

	return i2cDualStepperErrorE_Ok;
}

static enum i2cDualStepperError i2cDual_SetAccelerationDeceleration(
	struct i2cDualStepper* lpSelf,
	unsigned long int dwChannel,
	double lpAcceleration,
	double lpDeceleration
) {
	enum i2cError i2e;

	if(lpSelf == NULL) { return i2cDualStepperErrorE_InvalidParam; }
	if(dwChannel > 1) { return i2cDualStepperErrorE_InvalidParam; }

	uint8_t req[2+8];
	req[0] = i2cCmd_SetAccelerateDecelerate;
	req[1] = (uint8_t)dwChannel;

	serializeIEEE754SingleFloat_4Bytes((float)lpAcceleration, &(req[2]));
	serializeIEEE754SingleFloat_4Bytes((float)lpDeceleration, &(req[2+4]));

	i2e = i2cWrite(lpSelf->i2cBus, lpSelf->devAddr, req, sizeof(req));
	if(i2e != i2cE_Ok) { return i2cDualStepperErrorE_IOError; }

	return i2cDualStepperErrorE_Ok;
}

static enum i2cDualStepperError i2cDual_GetVMax(
	struct i2cDualStepper* lpSelf,
	unsigned long int dwChannel,
	double* lpVMax
) {
	enum i2cError i2e;

	if(lpSelf == NULL) { return i2cDualStepperErrorE_InvalidParam; }
	if(dwChannel > 1) { return i2cDualStepperErrorE_InvalidParam; }

	uint8_t req[2] = { i2cCmd_GetVMax, (uint8_t)dwChannel };
	uint8_t resp[4];

	/* Perform query */
	i2e = i2cWriteRead(lpSelf->i2cBus, lpSelf->devAddr, req, sizeof(req), resp, sizeof(resp));
	if(i2e != i2cE_Ok) { return i2cDualStepperErrorE_IOError; }

	if(lpVMax != NULL) { (*lpVMax) = (double)deserializeIEEE754SingleFloat_4Bytes(&(resp[0])); }

	return i2cDualStepperErrorE_Ok;
}

static enum i2cDualStepperError i2cDual_SetVMax(
	struct i2cDualStepper* lpSelf,
	unsigned long int dwChannel,
	double vMax
) {
	enum i2cError i2e;

	if(lpSelf == NULL) { return i2cDualStepperErrorE_InvalidParam; }
	if(dwChannel > 1) { return i2cDualStepperErrorE_InvalidParam; }

	uint8_t req[2+4];
	req[0] = i2cCmd_SetVMax;
	req[1] = (uint8_t)dwChannel;

	serializeIEEE754SingleFloat_4Bytes((float)vMax, &(req[2]));

	i2e = i2cWrite(lpSelf->i2cBus, lpSelf->devAddr, req, sizeof(req));
	if(i2e != i2cE_Ok) { return i2cDualStepperErrorE_IOError; }

	return i2cDualStepperErrorE_Ok;
}
static enum i2cDualStepperError i2cDual_GetAlpha(
	struct i2cDualStepper* lpSelf,
	unsigned long int dwChannel,
	double* lpAlpha
) {
	enum i2cError i2e;

	if(lpSelf == NULL) { return i2cDualStepperErrorE_InvalidParam; }
	if(dwChannel > 1) { return i2cDualStepperErrorE_InvalidParam; }

	uint8_t req[2] = { i2cCmd_GetAlpha, (uint8_t)dwChannel };
	uint8_t resp[4];

	/* Perform query */
	i2e = i2cWriteRead(lpSelf->i2cBus, lpSelf->devAddr, req, sizeof(req), resp, sizeof(resp));
	if(i2e != i2cE_Ok) { return i2cDualStepperErrorE_IOError; }

	if(lpAlpha != NULL) { (*lpAlpha) = (double)deserializeIEEE754SingleFloat_4Bytes(&(resp[0])); }

	return i2cDualStepperErrorE_Ok;
}
static enum i2cDualStepperError i2cDual_SetAlpha(
	struct i2cDualStepper* lpSelf,
	unsigned long int dwChannel,
	double alpha
) {
	enum i2cError i2e;

	if(lpSelf == NULL) { return i2cDualStepperErrorE_InvalidParam; }
	if(dwChannel > 1) { return i2cDualStepperErrorE_InvalidParam; }

	uint8_t req[2+4];
	req[0] = i2cCmd_SetAlpha;
	req[1] = (uint8_t)dwChannel;

	serializeIEEE754SingleFloat_4Bytes((float)alpha, &(req[2]));

	i2e = i2cWrite(lpSelf->i2cBus, lpSelf->devAddr, req, sizeof(req));
	if(i2e != i2cE_Ok) { return i2cDualStepperErrorE_IOError; }

	return i2cDualStepperErrorE_Ok;
}
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

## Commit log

2019-05-06 Added non-Arduino Version (if ARDUINO is not defined compiling works without Arduino libraries, if one wants to use Arduino IDE define ARDUINO as preprocessor variable
2019-05-07 Removed artifacts from Arduino libraries used during testing of the algorithm. The code now completely compiles without Arduino libraries with avr-gcc.
    Added I2C command definitions and I2C RX and TX queue handlers
    Implemented I2C commands (not tested):
    * i2cCmd_GetAccelerateDecelerate
    * i2cCmd_SetAccelerateDecelerate
    * i2cCmd_GetVMax
    * i2cCmd_SetVMax
    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
2019-05-07 Added support for constant speed and accelerated move steps functions via I2C
2019-05-07 Assigned correct operation to correct code
    [avr_dualsteppers.c]
2019-05-08 Added (work in progress) controller code for RaspberryPi
2019-05-08 Added currently available commands to command module. Verify serdes of floats!
2019-05-11 Fixed I2C problem
    Fixed the problem of I2C messages arriving during steppers
    running. The TIMER2_COMPA_VECT routine took too long for TWI
    events to be handeled as required. Stepper steps are now triggered
    by setting an timer expired flag in the TIMER2_COMPA_VECT and
    polling in the main loop - likewise for received TWI messages.
    Note that this of course means that there is always the potential
    of missing a single timer interrupt of timer 2 when doing longer
    processing (like recalculating constants) inside the TWI handler!
    [avr_dualsteppers.c]
2019-05-11 Some bugfixes (I2C transmit) and added support for exec commands for constant speed and accelerated relative movement
    [avr_dualsteppers.c]
2019-05-12 Patched I2C bug that prevented successful write-read transactions
    [001_accelerations.c, i2c.c]
2019-05-12 Reset fault state after readout
    [avr_dualsteppers.c]
2019-05-13 Added second test to include stepper shutdown request
2019-05-13 Added support to disable stepper drivers during idle periods and re-enable on next command
2019-05-14 Fixed microstepping setting, added hold support, some bugfixes
    [avr_dualsteppers.c]
2019-05-15 - Added support for acceleration / deceleration to constant speed (from a previously moving state) - State variables for steppers are not required to be volatile any more since motion control has bee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
2019-05-16 Added schematic for board using DIP packages as much as possible and DRV8825 breakout boards
2019-05-20 Added absolute positioning command and commands to read and write current absolute position
2019-05-22 Added first revision PCB layout
    [DualStepperI2C_PCB_2-B_Cu.gbr, DualStepperI2C_PCB_2-B_Mask.gbr, DualStepperI2C_PCB_2-B_Paste.gbr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]
2019-11-15 * Added some annotations for frama-c's wp and wp-rte plugin (workd in progress, unfinished) * Fixed 4 RTEs in handleTimer2Interrupt * Added frama-c working directory to gitignore
    [avr_dualsteppers.c]
2019-11-19 The following commands now delay their response till sufficient buffer space is available instead of failing silently:
    * i2cCmd_GetAlpha
    * i2cCmd_GetMicrostepping
    * i2cCmd_GetAbsolutePosition
    * i2cCmd_GetCommandQueueSize
    Continued ACSL annotation.
    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
    [avr_dualsteppers.c]
2019-11-20 Continued ACSL annotation for:
    * Various disjoint behaviors. They did use requires instead of assumes.
    * Added (incomplete) annotation to stepperSetup()
    * Added annotation for i2cRXDouble()
    * Added annotation for millis (modifies SREG, accesses systemMillis)
2019-11-20 ACSL: Added axioms for the first bunch of hardware registers as well as the loop invariant in the timer interrupt handler
2019-11-26 Recalculated constants, updated ACSL, fixed some bugs
    Proofed that RTE doesn't locate any bugs in stepperPlanMovement_ConstantSpeed
    and stepperPlanMovement_AccelerateStopToStop if called within specified
    boundaries.
    Updated constants to match new calculations.
    Updated ACSL to provide all necessary preconditions and postconditions
    for both functions
    [avr_dualsteppers.c]
2019-11-26 stepperPlanMovement_Disable: ACSL updated, all potential bugs located with RTE fixed
    [avr_dualsteppers.c]
2019-11-26 stepperPlanMovement_Stop: ACSL updated
2019-11-26 stepperPlanSpeedChange: ACSL updated
2019-11-27 Fixed ACSL assumption for PCINT1_vect, added exclusion of FRAMAC_SKIP to cli() and sei() to prevent clobbering of memory in inline assembly clobber list and added C variant of microDelay loop for ver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
    [avr_dualsteppers.c]
